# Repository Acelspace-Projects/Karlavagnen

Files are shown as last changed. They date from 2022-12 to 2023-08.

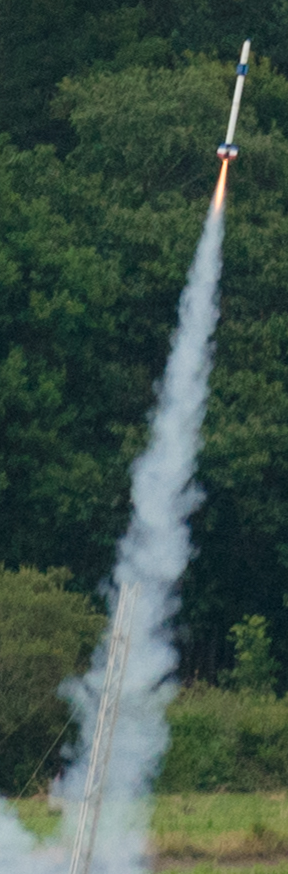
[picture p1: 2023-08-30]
Documentation/RapportDeProjet/img/Decollage.png

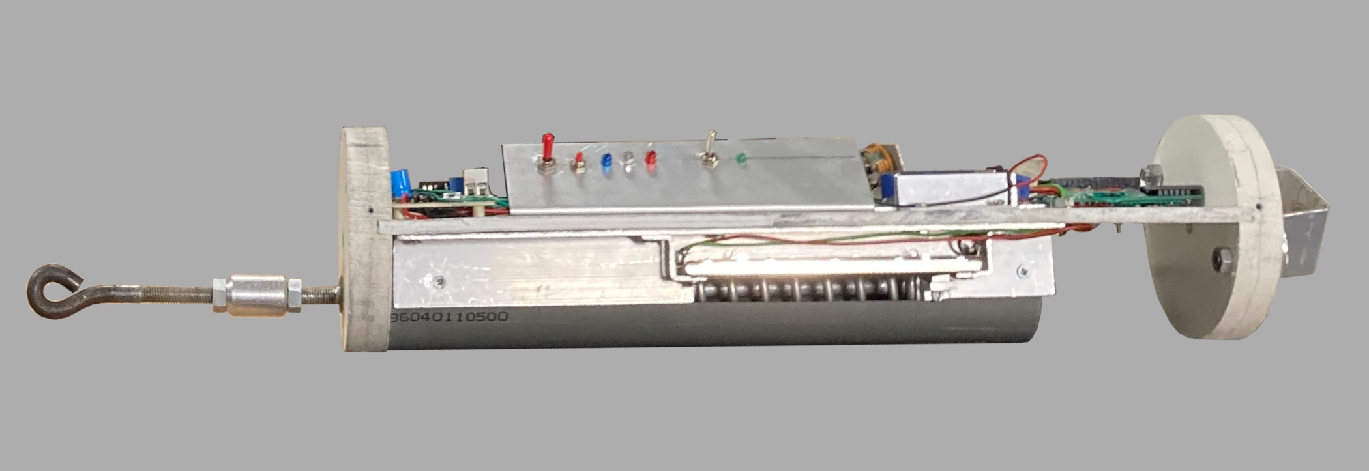
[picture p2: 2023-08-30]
Documentation/RapportDeProjet/img/Electronique1.png

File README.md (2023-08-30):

<h1 align="center">
    <br>
    <a href="https://github.com/Acelspace-Projects/Karlavagnen">
        Acelspace logo
    </a>
    <br>
    <b>Karlavagnen</b>
</h3>

<h3 align="center">
    Ceci est un dépot pour le projet Fusex Karlavagnen utilisé pour le versionning et pour avoir des backups.
</h3>

<div class="badges" align="center">
    
    
</div>

---

### Description
Karlavagnen embarquait en 2023 une expérience de mesure de tension sur les sangles du parachute, deux mesures de vitesse (pitot et venturi), une mesure d'altitude (BMP180), une carte de prise de mesures et de télémesure CATS systems ainsi qu'une caméra intégrée à l'ogive.

### Liens
- [StabTraj](https://github.com/Acelspace-Projects/Karlavagnen/blob/main/Documentation/StabTraj/ST-(StabTraj)_KARLAVAGNEN.xlsx)
- [Dossier de définition](https://github.com/Acelspace-Projects/Karlavagnen/blob/main/Documentation/DossierDeDefinition/DDD_KARLAVAGNEN.pdf)
- [Dossier technique](https://github.com/Acelspace-Projects/Karlavagnen/blob/main/Documentation/DossierTechnique/DT_KARLAVAGNEN.pdf)
- [Rapport de projet](https://github.com/Acelspace-Projects/Karlavagnen/blob/main/Documentation/RapportDeProjet/RP_KARLAVAGNEN.pdf)

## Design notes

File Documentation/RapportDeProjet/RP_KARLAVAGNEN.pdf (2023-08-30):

Rapport de projet | – | Karlavagnen | FX04 | – | 27/08/23

# RAPPORT DE PROJET KARLAVAGNEN

2023

# BENAY Clément CHAUVIN Geoffroy FAJAL Dimitri KAE-NUNE Damien LORIN DE LA GRANDMAISON Alexandre LORIN DE LA GRANDMAISON Clément PINGLIER Etienne

Karlavagnen | FX04 | – | 1/14

# SOMMAIRE

## I. Présenstation de l’équipe ____________ Page 3

1) Présentation générale | Page 3
2) Les membres de l’équipe | Page 3

## II. Présentation de Karlavagnen _________ Page 4 III. Plan Général _______________________ Page 5 IV. Conception mécanique ________________ Page 6

1) Informations générales | Page 6
2) Montage des ailerons | Page 6
3) Système de retenue du propulseur | Page 6

## V. Système d’éjection ___________________ Page 7

1) Plan mécanique | Page 7
2) Plan électrique (séquenceur) | Page 7

## VI. Expériences (Tensionomètre, mesures de vitesse et caméra) ______________________ Page 8

1) Tensionomètre | Page 8
2) Mesures de vitesse | Page 9
3) Caméra | Page 10

## VII. Résultats et exploitation _________ Page 11

1) Rapport de vol | Page 11
2) Exploitation des données | Page 12
1. Caméra: | Page 12
2. Tensionomètre: | Page 12
3. Capteurs de vitesse: | Page 13
4. Capteur de Pression: | Page 13
Karlavagnen | FX04 | – | 2/14

# 1) PRÉSENTATION GÉNÉRALE

Notre groupe était constitué de 7 lycéens issus de 2 lycées de région parisienne (lycée Sonia Delaunay et lycée La Bruyère). Nous étions presque tous en Terminale et un des participant était en Seconde.
Nous avions déjà mené plusieurs projets auparavant dont un projet Fusex nommé OGMA. Chaque membre avait préalablement mené à bien plusieurs projets et avait donc de l’expérience en terme de conception, d’électronique, de mécanique ou même en programmation. Nous étions encadrés par Roger POISSON, vétéran du C’SPACE et habitué des projets fusées et Sylvain BEAU, ingénieur.

# 2) LES MEMBRES DE L’ÉQUIPE

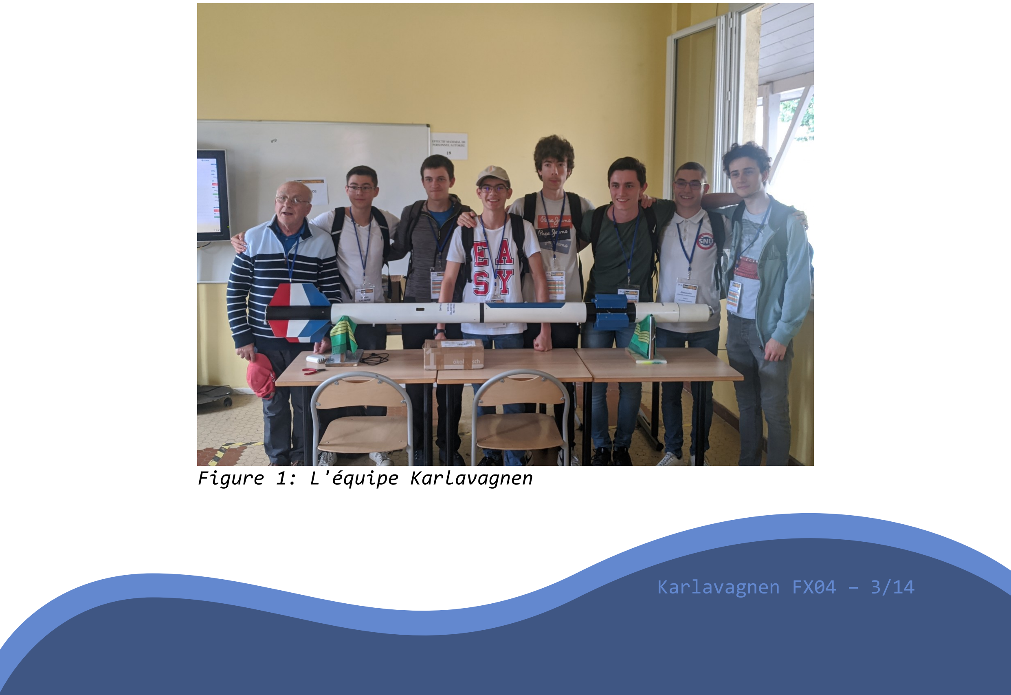
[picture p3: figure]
Karlavagnen; Figure 1: L'équipe Karlavagnen

Le projet KARLAVAGNEN repartait des connaissances acquises avec le projet OGMA, il avait ainsi pour but d’améliorer les expériences qui s’y trouvaient. Cette Fusex contenait donc notament une mesure de la tension aux sangles du parachute (avec le système que l’on a appelé «Tensionomètre»).
Toutefois, de nouvelles expériences ont été ajoutées, avec notamment l’ajout d’un bloc de mesure de vitesse à travers deux manières différentes (pitot et venturi), ainsi que d’une caméra pour filmer l’entièreté du vol. Elle contenait également une carte d’acquisition de mesure et de télémesure “CATS”. Enfin, des mesures d’altitudes ont été effectuées dans le but de les comparer avec les valeurs théoriques de l’altitude données par le StabTraj.

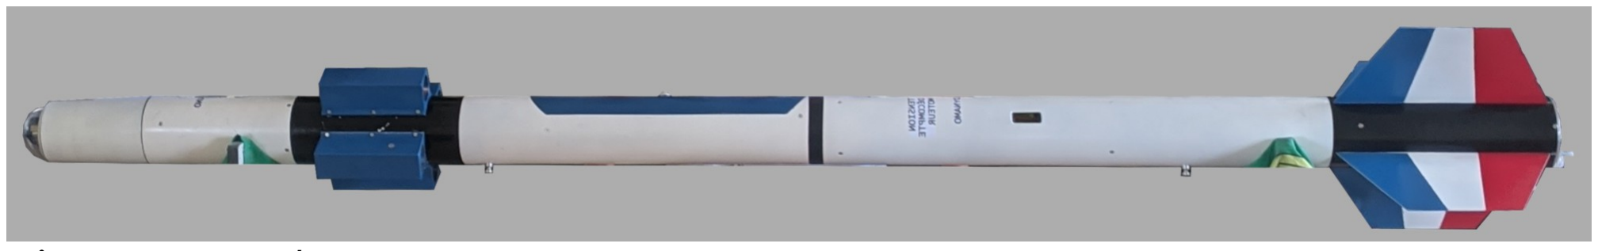
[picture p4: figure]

Figure 2: Karlavagnen

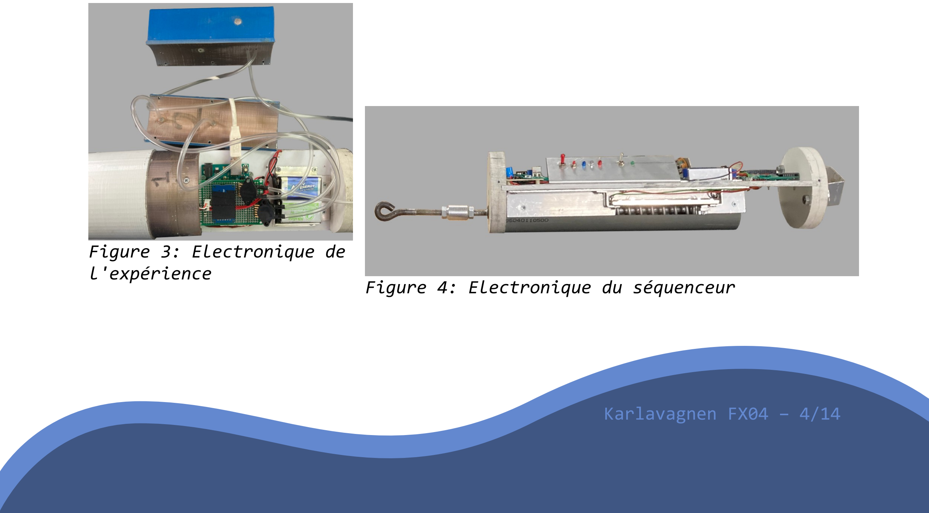
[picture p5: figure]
Karlavagnen; Figure 3: Electronique de l'expérience; Figure 4: Electronique du séquenceur

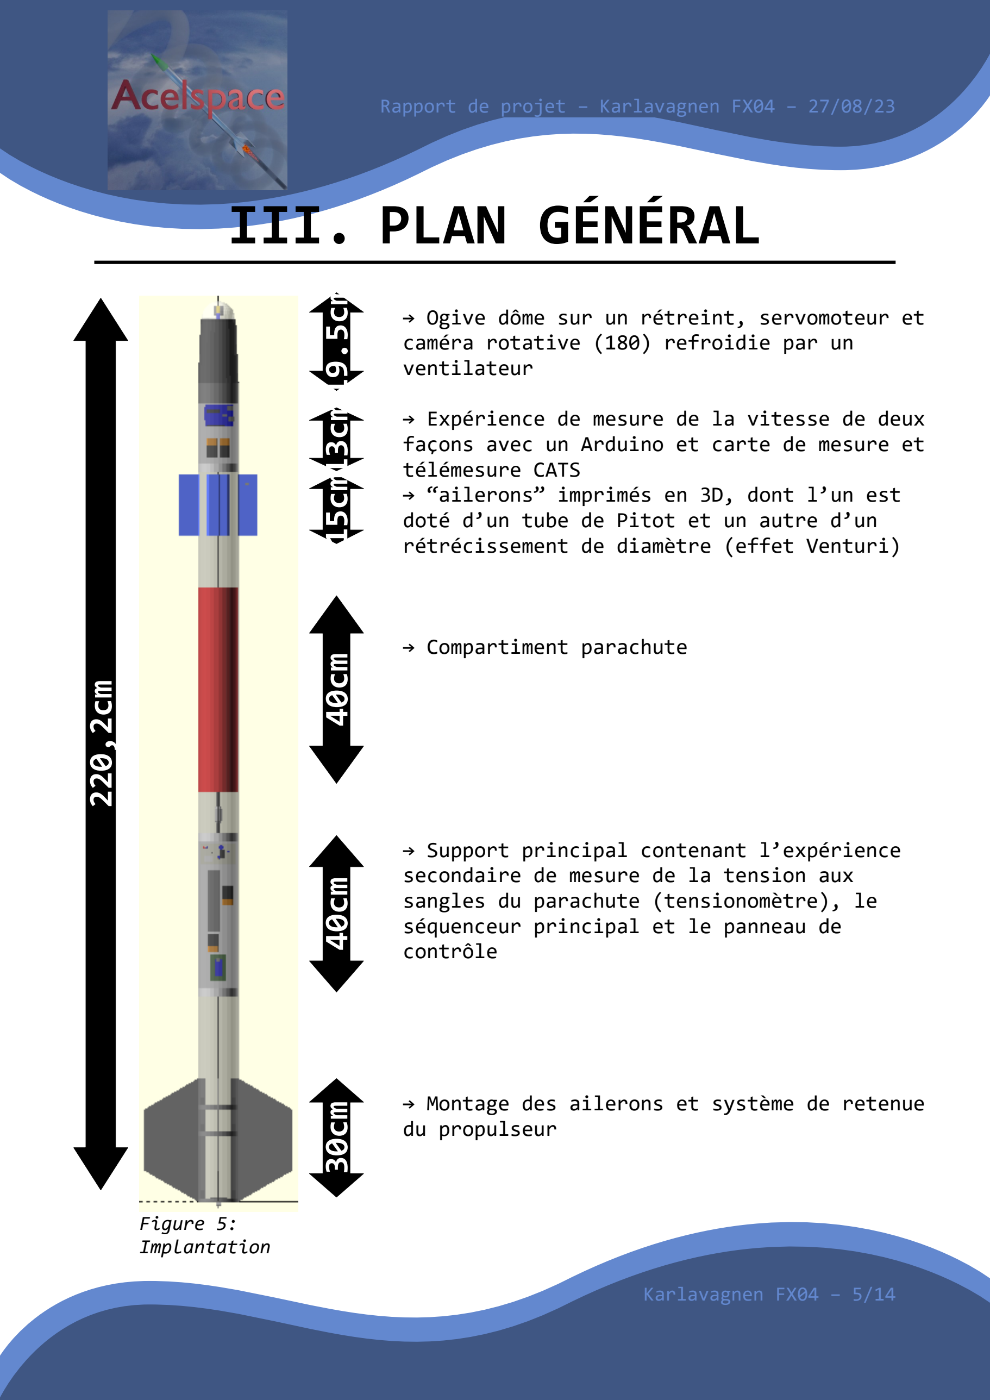
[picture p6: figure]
III. PLAN GÉNÉRAL; Karlavagnen; caméra rotative (180) refroidie par un ventilateur; télémesure CATS; rétrécissement de diamètre (effet Venturi); → Compartiment parachute; → Support principal contenant l’expérience secondaire de mesure de la tension aux sangles du parachute (tensionomètre), le séquenceur principal et le panneau de contrôle; du propulseur; Figure 5: Implantation

→ Ogive dôme sur un rétreint, servomoteur et

→ Expérience de mesure de la vitesse de deux façons avec un Arduino et carte de mesure et

→ “ailerons” imprimés en 3D, dont l’un est doté d’un tube de Pitot et un autre d’un

→ Montage des ailerons et système de retenue

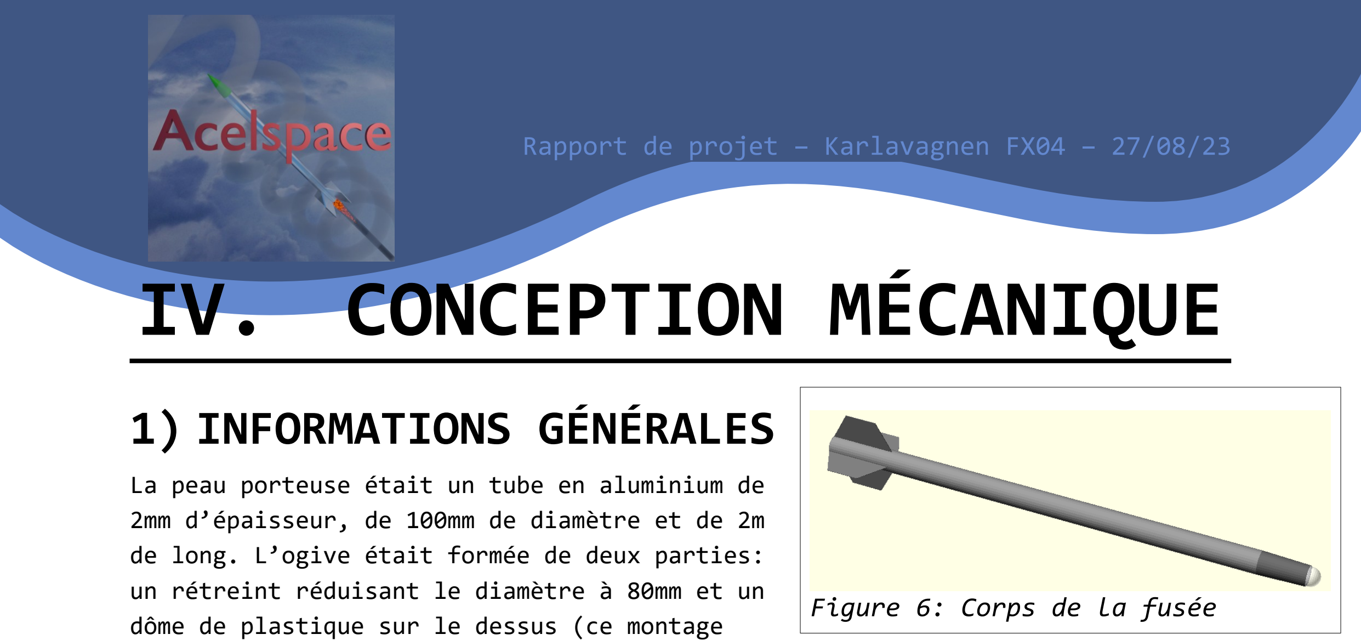
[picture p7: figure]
IV. CONCEPTION MÉCANIQUE; 1) INFORMATIONS GÉNÉRALES; Figure 6: Corps de la fusée

Rapport de projet – Karlavagnen FX04 – 27/08/23

La peau porteuse était un tube en aluminium de 2mm d’épaisseur, de 100mm de diamètre et de 2m de long. L’ogive était formée de deux parties: un rétreint réduisant le diamètre à 80mm et un dôme de plastique sur le dessus (ce montage permettait l’installation de la caméra). Le tout mesurait 19,5 cm en hauteur.

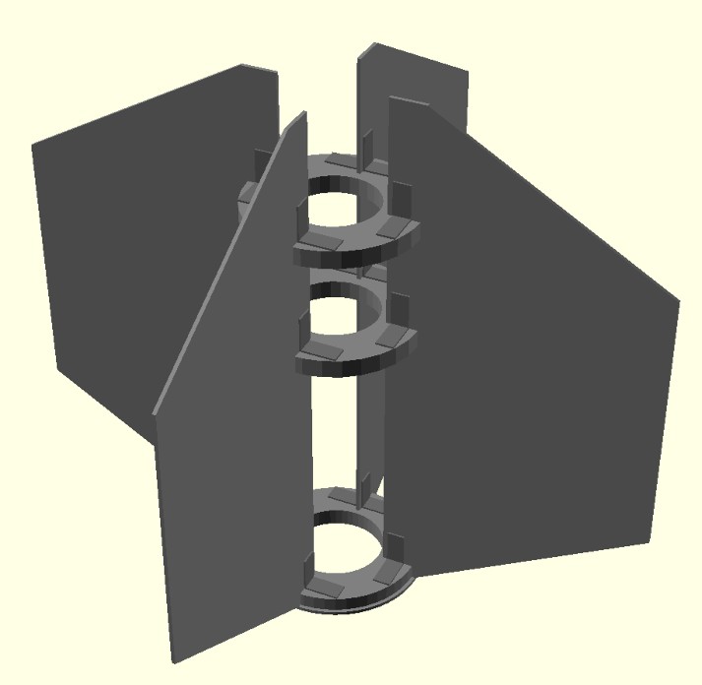
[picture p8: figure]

# 2) MONTAGE DES AILERONS

Les ailerons été attachés à trois bagues en aluminium à l’aide d’équerres de métal.
Le montage complet était accroché au tube avec des vis. La bague la plus inférieure était la plaque de poussée. Elle transférait la poussée du propulseur au corps de la fusée.

# 3) SYSTÈME DE RETENUE DU PROPULSEUR

Le propulseur était retenu par un petit montage en métal accroché à la plaque de poussée.
Celui-ci était construit à l’aide d’un “Sandwich” de pièces en aluminium usinées.
Pour monter le propulseur, il suffisait de l’insérer dans le corps de la fusée. Lorsqu’il était bien monté, un petit “clic” était audible lorsque le pêne ressortait du montage.
Pour enlever le propulseur, il suffisait de pousser la poignée avec le doigt. Étant accroché au pêne il relâchait le propulseur qui pouvait alors être retiré.

Karlavagnen FX04 – 6/14

Figure 8: Sytème de
retenue du propulseur

Pêne

Poignée

Figure 7: Montage des
ailerons

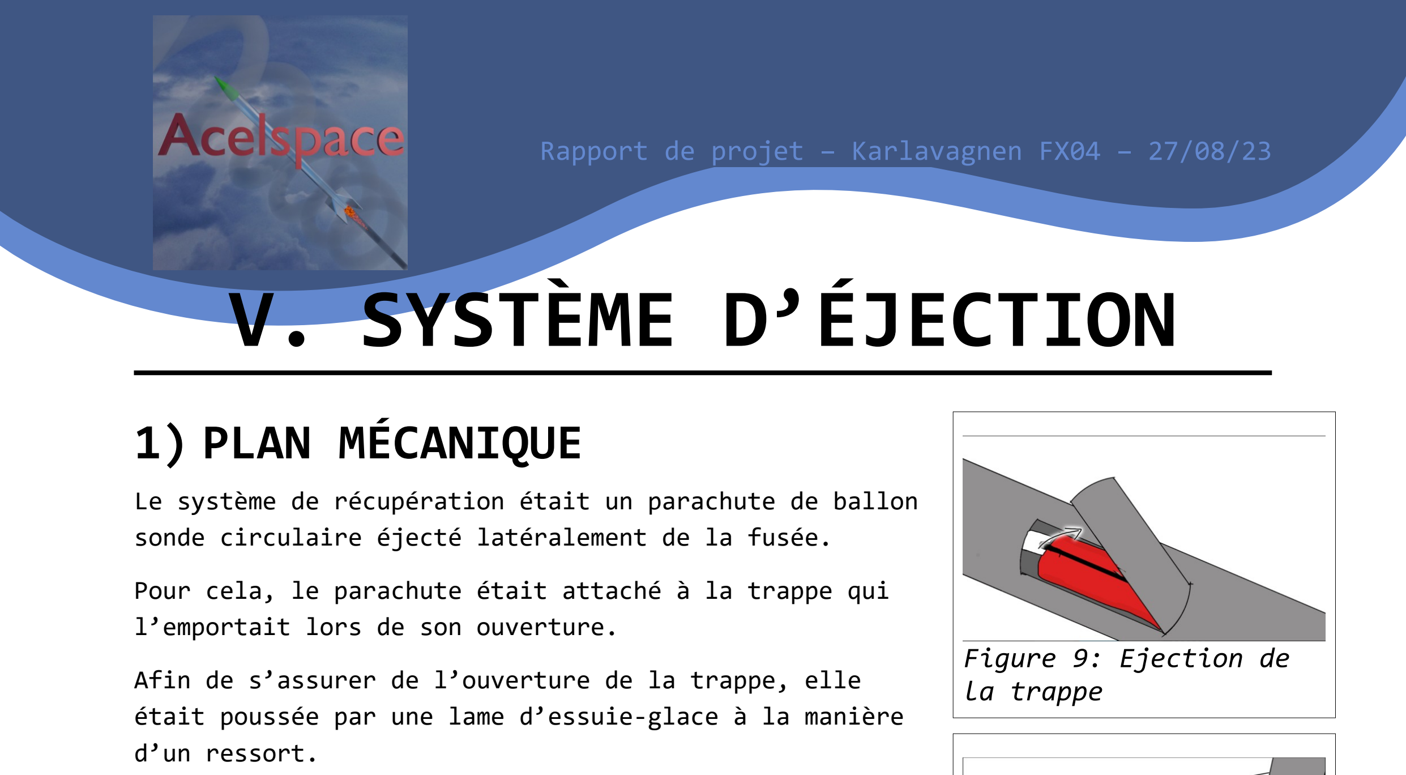
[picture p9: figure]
V. SYSTÈME D’ÉJECTION; 1) PLAN MÉCANIQUE; l’emportait lors de son ouverture.; d’un ressort.; Figure 9: Ejection de la trappe

Le système de récupération était un parachute de ballon sonde circulaire éjecté latéralement de la fusée.
Pour cela, le parachute était attaché à la trappe qui

Afin de s’assurer de l’ouverture de la trappe, elle était poussée par une lame d’essuie-glace à la manière

# 2) PLAN ÉLECTRIQUE (SÉQUENCEUR)

Une minuterie analogique soudée par nos soins permettait
le décompte de l’ouverture de la trappe. Un peu avant
l’apogée, le séquenceur enclenchait un moteur. Sur celui-ci était accroché une cloche qui en tournant libérait alors la trappe.

Figure 10: Sortie du
parachute

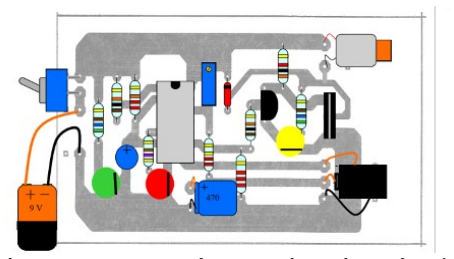
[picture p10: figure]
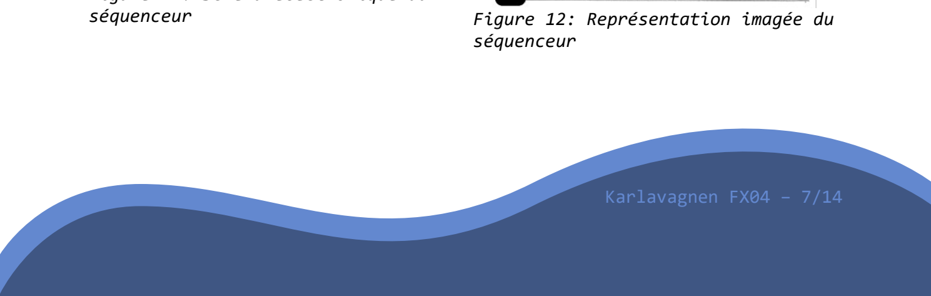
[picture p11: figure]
Karlavagnen; séquenceur; Figure 12: Représentation imagée du

Figure 11: Schéma électronique du

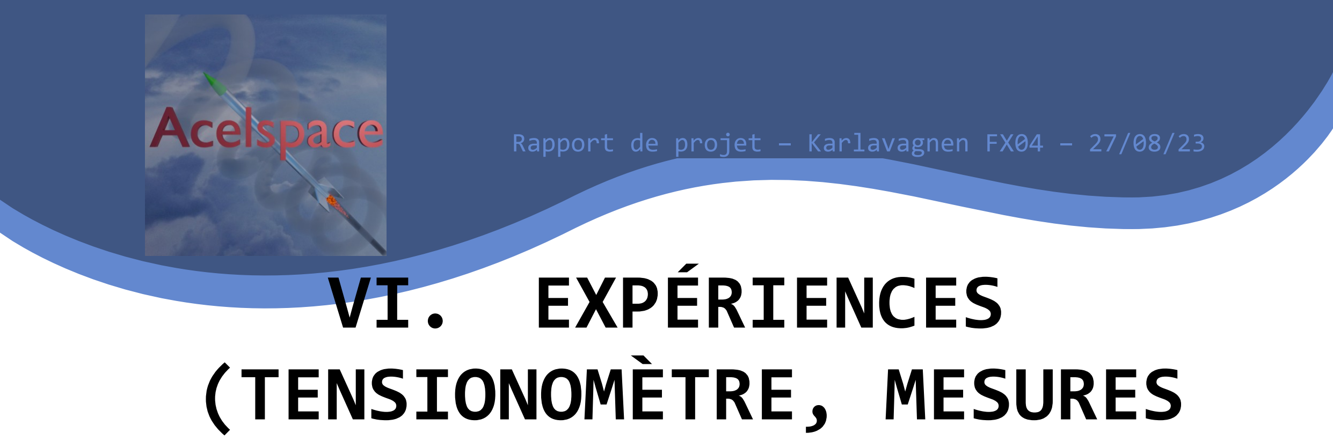
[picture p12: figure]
VI. EXPÉRIENCES (TENSIONOMÈTRE, MESURES

# DE VITESSE ET CAMÉRA)

# 1) TENSIONOMÈTRE

La tension était mesurée sur les sangles du parachute. Deux ressorts de 15cm chacun étaient compressés par la sortie du parachute. Ainsi le potentiomètre linéaire relié à un Arduino permettait d’effectuer l’acquisition des données qui étaient sauvegardées en temps réel sur carte microSD.

Après le vol, les données furent récupérées et passées au travers d’une fonction de conversion qui transformait les données brutes (de 0 à 1023 données par la carte arduino) en données exploitables (force exercée en kg). Celle-ci était déterminée en appliquant des masses connues (poids d’haltère et autres)

Figure 13: Le système est le même que l'an dernier à la différence qu'il sera maintenant composé de deux ressorts pour une plus grande résistance (1000 N) et qu'il n'est plus aligné avec la sangle (il faut maintenant une poulie dans la trappe)

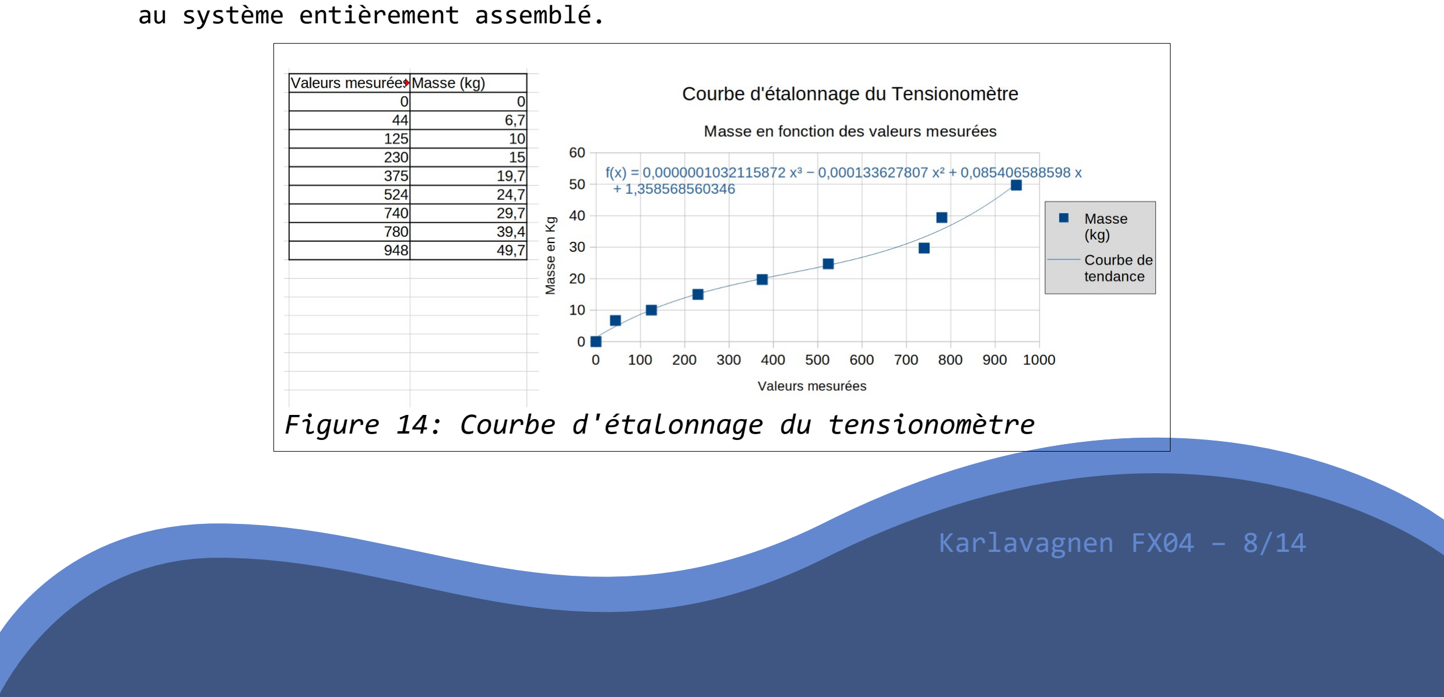
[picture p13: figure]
au système entièrement assemblé.; Karlavagnen

Figure 14: Courbe d'étalonnage du tensionomètre

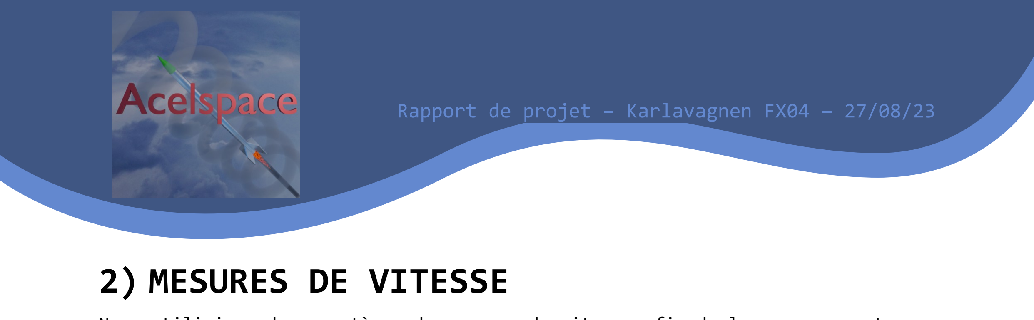
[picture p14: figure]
2) MESURES DE VITESSE

Rapport de projet – Karlavagnen FX04 – 27/08/23

Nous utilisions deux systèmes de mesures de vitesse afin de les comparer. Le premier utilisait un tube de Pitot et le second exploitait l’effet venturi. Les deux systèmes étaient montés sur un support en PVC et les données étaient compilées grâce à une carte Arduino, puis enregistrées sur carte SD.

Sur le tube étaient placés quatre “ailerons” dont deux contenaient les tubes de mesures qui acheminaient l’air jusqu’aux MPX5010DP, capteurs différentiels de pression permettant le calcul de vitesse. Les deux autres permettaient simplement d’assurer la stabilité et étaient passifs.

Figure 17: Tube de
pitot

Figure 15: Tube de
venturi

Figure 16: "Ailerons"
permettant les mesures

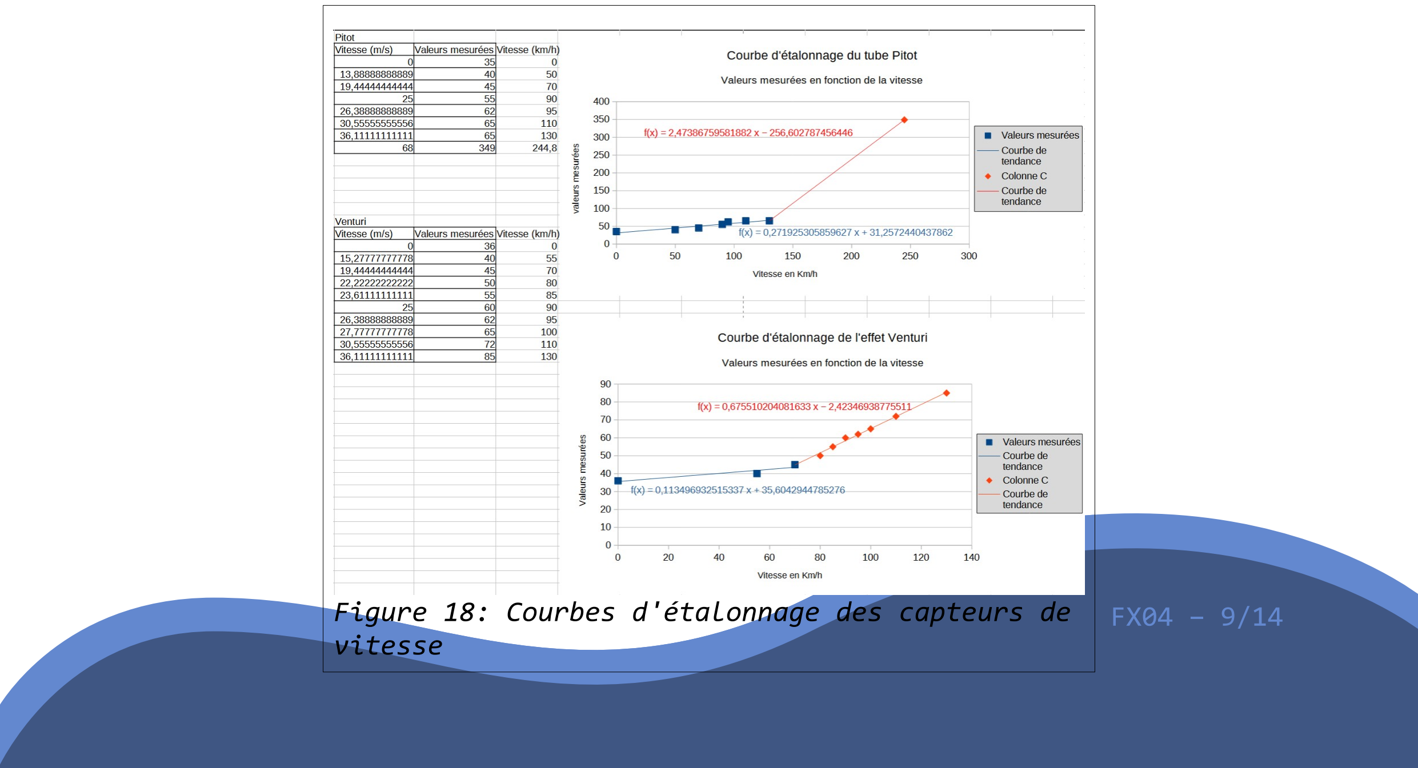
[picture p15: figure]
Karlavagnen; vitesse

Figure 18: Courbes d'étalonnage des capteurs de

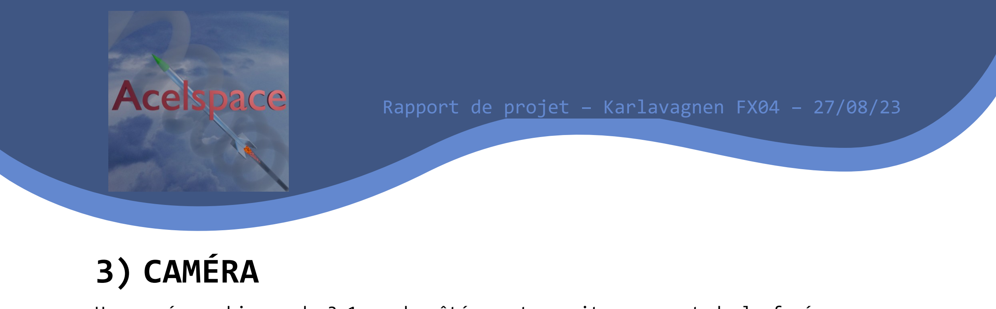
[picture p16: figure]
3) CAMÉRA

Une caméra cubique, de 3.1 cm de côté, se trouvait au sommet de la fusée, protégée par un dôme de plexiglas. Les images ont été enregistrées sur une carte microSD. Un système de servomoteur, faisant des aller-retours entre 0° et 180°, permettait de l’orienter.
Ayant remarqué une perte de performance de la caméra lorsqu’elle surchauffait, nous avions décidé d’installer un ventilateur dans le dôme.

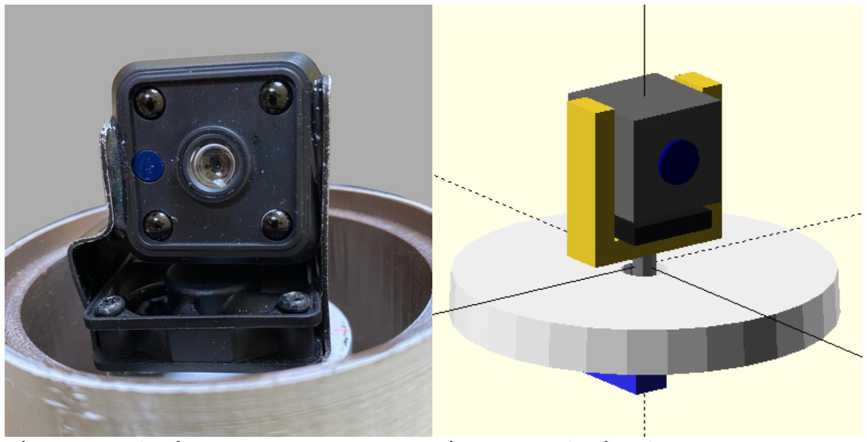
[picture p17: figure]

Figure 19: Caméra IRL | Figure 20: Caméra 3D

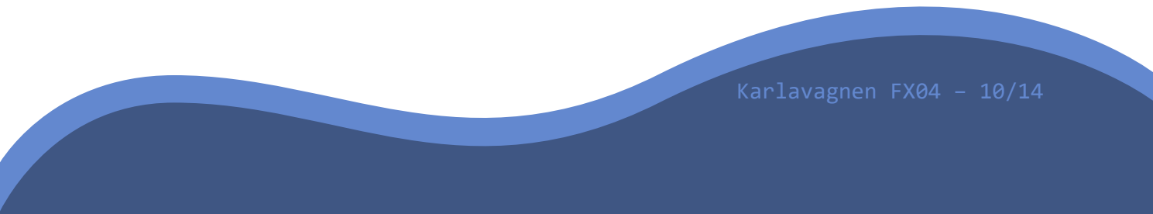
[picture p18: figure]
Karlavagnen

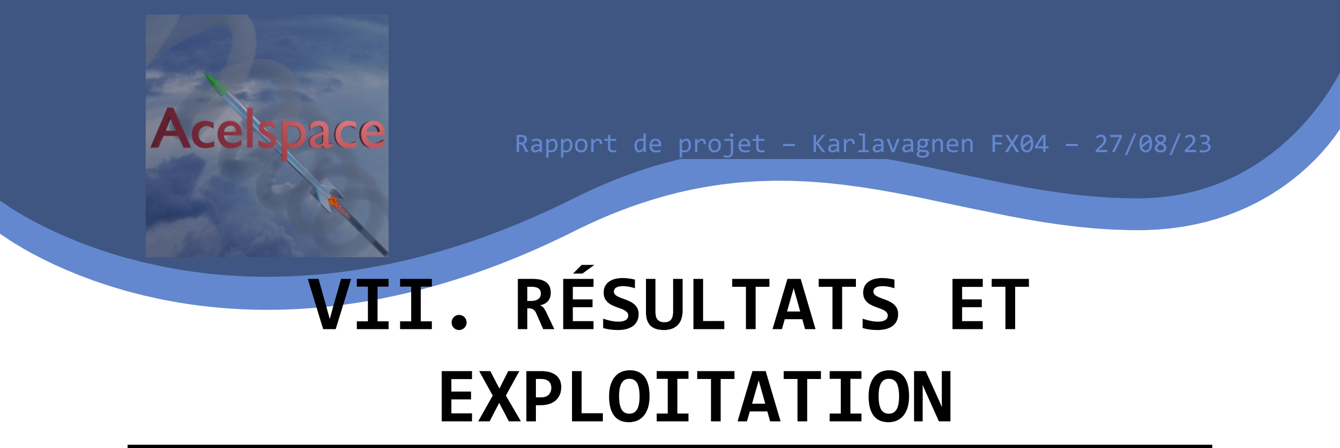
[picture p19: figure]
VII. RÉSULTATS ET EXPLOITATION

# 1) RAPPORT DE VOL

La fusée a été lancée le 19 juillet 2023, le plafond nuageux étant relativement bas, il n’a pas été possible de suivre l’entièreté du vol.
La fusée a cependant effectué un vol nominal et toutes les mesures ont été enregistrées avec succès.
Lors de la récupération, la fusée s’était posée dans un buisson de ronces ce qui l’a amortie à l’atterissage. Grâce à ça, la fusée était donc intacte.

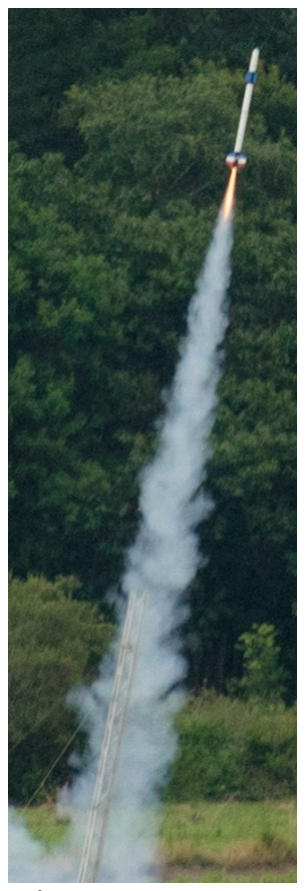
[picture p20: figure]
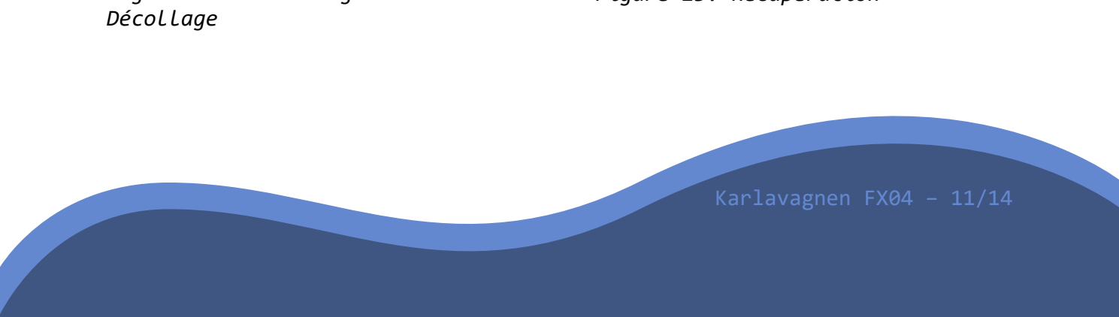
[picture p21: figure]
Karlavagnen; Décollage

Figure 21:

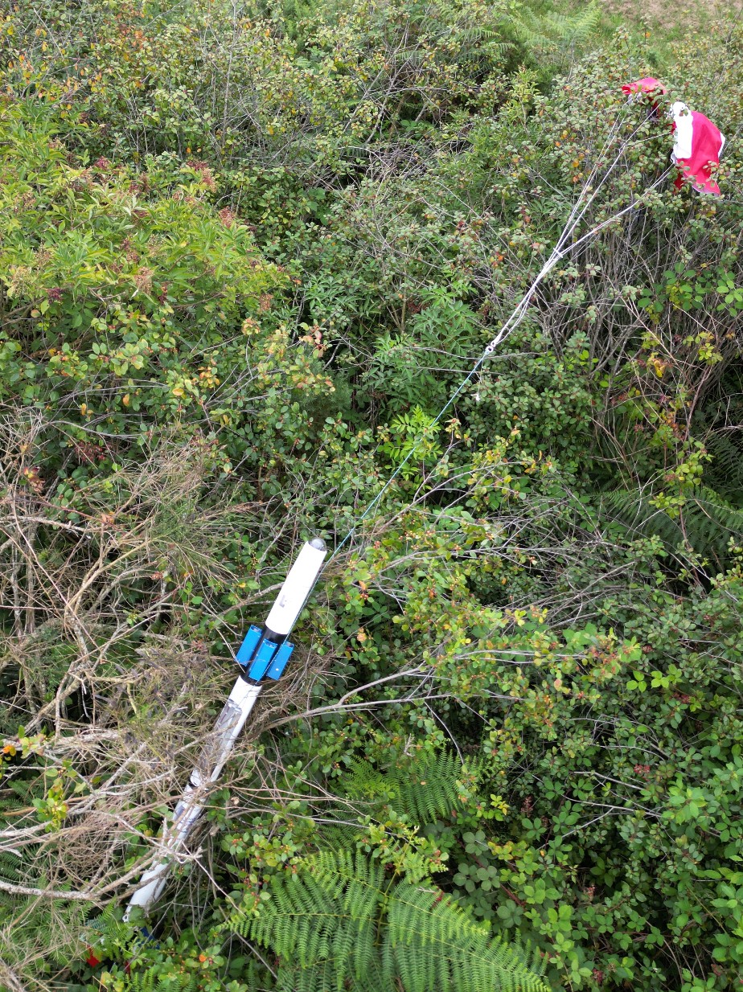
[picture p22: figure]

Figure 22: Descente Figure 23: Récupération

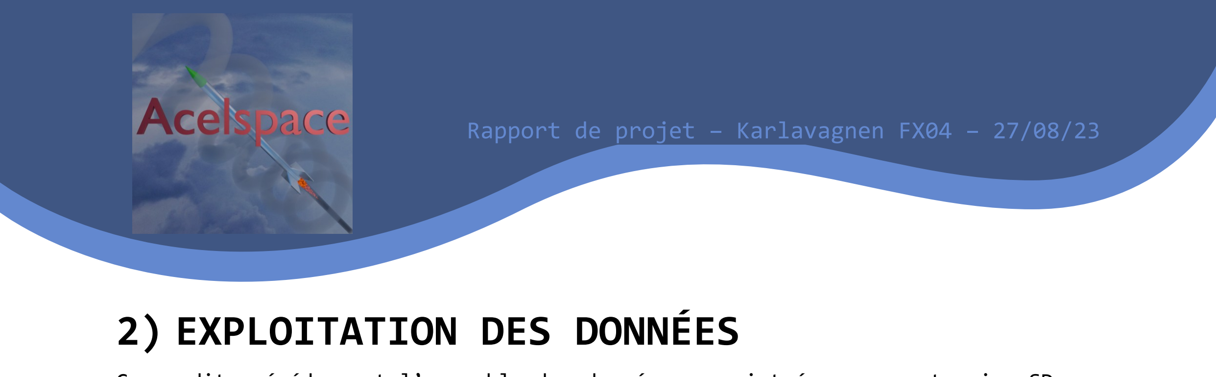
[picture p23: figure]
2) EXPLOITATION DES DONNÉES

Comme dit précédemment l’ensemble des données enregistrées sur carte microSD ont été récupérées. Après utilisation d’un logiciel tableur, les graphes ci-dessous ont été établis.

### 1. CAMÉRA:

La vidéo de la caméra est complète et sans coupures et sectionnée en fichiers de 1 minute (comme prévu). Suite au décollage on peut y voir la fusée monter et s’engouffrer dans les nuages au bout de 8 secondes.

### 2. TENSIONOMÈTRE:

En observant le graphe représentant la force exercée sur les sangles du parachute en fonction du temps écoulé, nous pouvons noter deux choses:
- La vitesse d’acquisition (20Hz) était trop lente et la courbe obtenue présente, en conséquence, un manque de précision lors de la sortie du parachute (deux points seulement montrent l’évolution de la force autour du pic).
- Le capteur a dû être mal dimensionné et en conséquence est arrivé en butée. La valeur max étant 60kg.

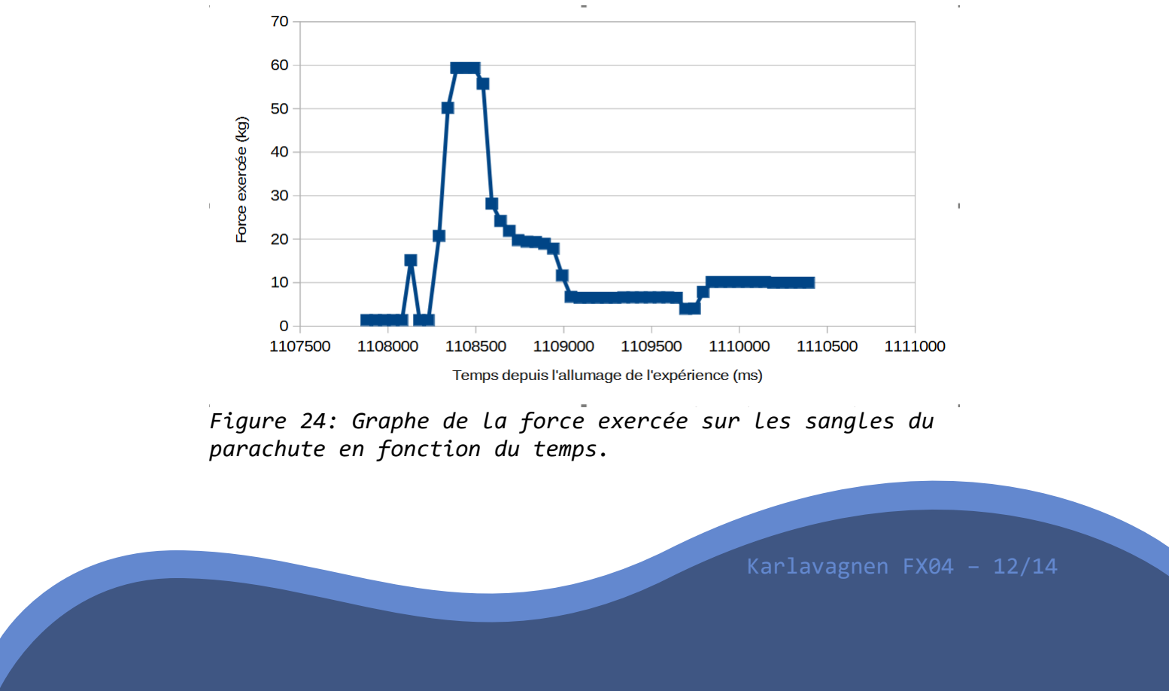
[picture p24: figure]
Karlavagnen; parachute en fonction du temps.

Figure 24: Graphe de la force exercée sur les sangles du

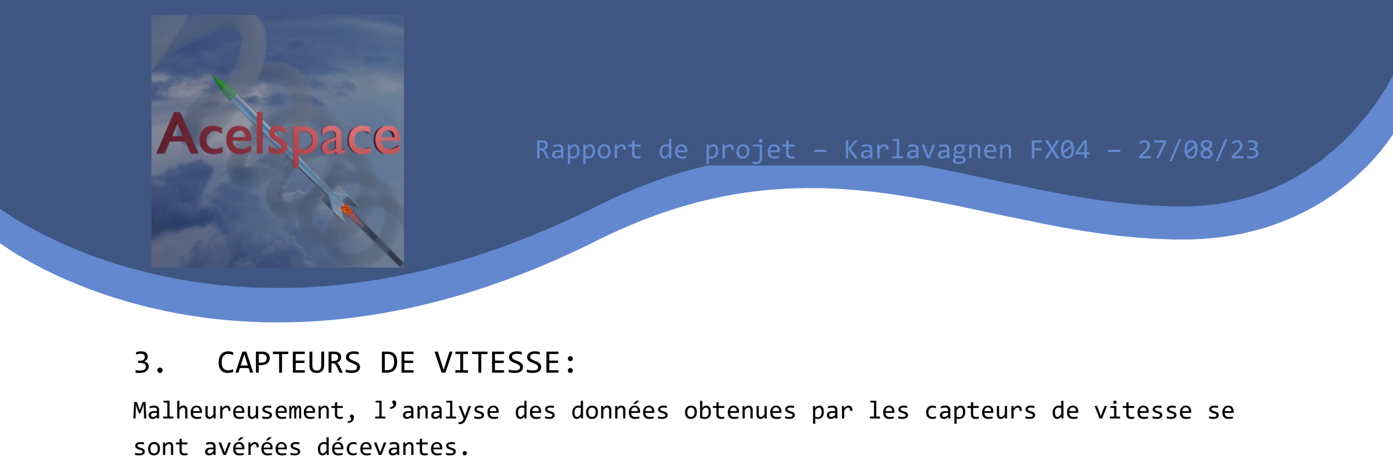
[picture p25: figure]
3. CAPTEURS DE VITESSE:; sont avérées décevantes.

Malheureusement, l’analyse des données obtenues par les capteurs de vitesse se

Tout d’abord le capteur pour la mesure de la vitesse par tube de pitot n’a retourné que des valeurs correspondant à sa butée minimale, ce qui correspond à une erreur de branchement des tuyaux de pression. Pourtant, le sens de branchement était bien connu, mais la présence d’un détrompeur sur le mauvais tuyau a mené un membre de l’équipe à le rebrancher sur la mauvaise entrée du capteur.
Enfin, bien que le capteur utilisant l’effet venturi ait rendu des valeurs, le graphe a révélé la présence de fortes perturbations dans les mesures. Celle-ci sont très probablement liées à des turbulences dans le capteur à cause de la prise aérodynamique des “ailerons”.
L’ensemble des mesures de ces capteurs sont donc inexploitables.

### 4. CAPTEUR DE PRESSION:

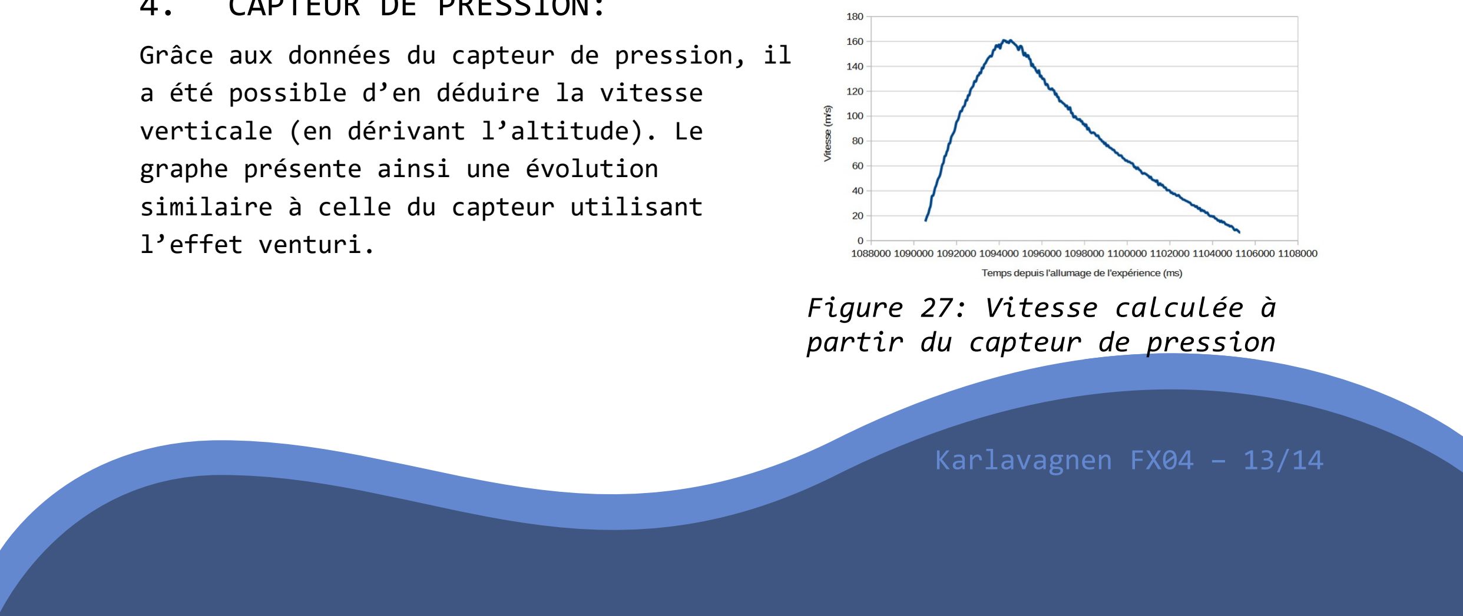
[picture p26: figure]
a été possible d’en déduire la vitesse verticale (en dérivant l’altitude). Le graphe présente ainsi une évolution similaire à celle du capteur utilisant l’effet venturi.; Karlavagnen; Figure 27: Vitesse calculée à partir du capteur de pression

Grâce aux données du capteur de pression, il

Figure 26: Mesures brutes et moyenne à trois points du capteur de Venturi

Figure 25: Mesures brutes du capteur
de Pitot

Le capteur également a pu nous montrer que l’altitude à l’apogée prévue par le StabTraj était grandement surestimée (On s’attendait à une apogée à 1400m mais avons obtenue une apogée à 1200m). Cet écart peut probablement s’expliquer par une mauvaise évaluation du Cx de la fusée, notée à 0.6 dans le StabTraj. Pour faire correspondre les données du StabTraj aux données obtenues il aurait fallu mettre un Cx à 0.85.

# REMERCIEMENTS

“ Karlavagnen est en fait le dernier projet que nous avons réalisé ensemble avant de nous diriger dans nos écoles respectives. Il nous sera donc impossible de réaliser tous ensemble un autre projet.
C’est pour cela que je tenais à remercier tous les membres du groupe de s'être investis dans le projet afin qu'il arrive à complétion. Malgré les problèmes de conception et la difficulté de réalisation, tout le monde a donné de soi et de son temps pour assurer un vol nominal en créant un projet de qualité.
Merci particulièrement à Roger et à Sylvain pour nous avoir accompagnés et aidés lorsque des difficultés se sont présentées, et de nous avoir éclairés de

Et merci à l’équipe de Planète Science de nous avoir permis de vivre ‘une expérience pour les jeunes’. ”, Dimitri FAJAL

Figure 28: Altitude en fonction du temps

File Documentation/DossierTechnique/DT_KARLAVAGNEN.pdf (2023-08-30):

Dossier Technique Karlavagnen – Karlavagnen FX04 – 2023-08-27

# DOSSIER TECHNIQUE KARLAVAGNEN

2023

# FAJAL Dimitri CHAUVIN Geoffroy LORIN DE LA GRANDMAISON Clément LORIN DE LA GRANDMAISON Alexandre BENAY Clément KAE-NUNE Damien PINGLIER Etienne

Karlavagnen FX04 – 1/8

# SOMMAIRE

## I. Plan général _________________________ Page 3 II. Conception mécanique ________________ Page 4

1) Informations générales | Page 4
2) Montage ailerons | Page 4
3) Système de retenue du propulseur | Page 4

## III. Système d’éjection _________________ Page 5

1) Plan mécanique | Page 5
2) Plan électrique (séquenceur) | Page 5

## IV. Expériences (Tensionomètre, mesures de vitesse et caméra) ______________________ Page 6

1) Tensionomètre | Page 6
2) Mesures de vitesse | Page 7
3) Caméra | Page 7

# I. PLAN GÉNÉRAL

Xmm; Figure 1: Implantation

→ Ogive dôme sur un rétreint, servomoteur et caméra rotative (180) soutenue par un ventilateur

→ Minuterie secondaire : Arduino xpérience de mesure de la vitesse de deux façons afin de les comparer

→ Parallélépipèdes imprimés en 3D, dont l’un est doté d’un tube de Pitot et un autre d’un rétrécissement de diamètre (effet Venturi)

→ Trappe d’éjection du parachute

→ Support principal contenant l’expérience secondaire de mesure de la tension aux sangles du parachute (tensionomètre), le séquenceur principal et le panneau de contrôle

→ Montage des ailerons et système de retenue du propulseur

Nous utilisons un total de 5 piles 9V : trois dans la minuterie secondaire et deux dans la minuterie principale.

# II. CONCEPTION MÉCANIQUE

# 1) INFORMATIONS GÉNÉRALES

La peau porteuse est un tube en aluminium de 2mm d’épaisseur, de 100mm de diamètre et de 2m de long. Elle offre une grand solidité. L’ensemble des montages à l’intérieur sont solidement
accroché au tube par des vis.


L’ogive est formée de deux parties : un rétreint réduisant le diamètre à 80mm et un dôme de plastique sur le dessus (ce montage permet l’installation d’une caméra). Le tout mesure 19,5 cm en hauteur.


# 2) MONTAGE AILERONS

Les ailerons sont attachés à trois bagues en aluminium à l’aide d’équerres de métal.
Le montage complet est accroché au tube par avec des vis. La bague la plus inférieure est la plaque de poussée.
Elle transfère la poussée du propulseur au corps de la
fusée.

# 3) SYSTÈME DE RETENUE DU PROPULSEUR

Le propulseur est retenu par un petit montage en métal
accroché à la plaque de poussée.
Celui-ci est construit à l’aide d’un « Sandwich » de pièces en aluminiums usinées.
Pour monter le propulseur, il suffit de l’insérer dans le corps de la fusée. Lorsqu’il est bien montée, un petit « clic » est audible lorsque la pêne ressort du montage.
Pour enlever le propulseur, il faut pousser la poignée avec le doigt. Étant accroché à la pêne il relâchera le propulseur qui peut alors être retiré.

Pêne

Figure 4: Sytème de retenue du propulseur

Poignée

Figure 3: Montage des
ailerons

Figure 2: Corps de la fusée

# III. SYSTÈME D’ÉJECTION

# 1) PLAN MÉCANIQUE

Le système de récupération est un parachute de ballon sonde circulaire éjecté latéralement de la fusée. Pour cela, il est attaché à la trappe qui l’emporte lors de son ouverture. Afin de s’assurer de l’ouverture de la


trappe, elle est poussée par une lame d’essuie-glace à la manière d’un ressort.

# 2) PLAN ÉLECTRIQUE (SÉQUENCEUR)

Une minuterie analogique soudée par nos soins permet le décompte de l’ouverture de la trappe. Un peu avant


l’apogée, le séquenceur enclenche un moteur. Sur celui-ci est accroché une cloche qui en tournant libère la trappe.

Figure 5: Ejection de la
trappe

Figure 6: Sortie du
parachute


Figure 7: Schéma électronique du


séquenceur | Figure 8: Représentation imagée du séquenceur

# IV. EXPÉRIENCES (TENSIONOMÈTRE, MESURES DE VITESSE ET CAMÉRA)

# 1) TENSIONOMÈTRE

La tension sera mesurée sur les sangles du parachute. Deux ressorts de 15cm chacun sont compressés par de la sortie du parachute. Ainsi le potentiomètre linéaire relié à un Arduino permettent d’effectuer l’acquisition des données qui sont sauvegardées en temps réel sur carte microSD.

Après vol, les données sont récupérées et passées au travers d’une fonction de conversion qui transforme les données brutes (de 0 à 1023 données par la carte arduino) en donées exploitables (force exercée en kg).
Cette fonction de conversion est déterminée en appliquant des masses connues (poids d’altère et autres) au système entièrement assemblé. Une courbe d’étalonnage est alors établie sur un tableur pour ensuite faire apparaître la courbe de tendance dont l’équation est la fonction de conversion.

Figure 9: Le système est le même que l'an dernier à la différence qu'il sera maintenant composé de deux ressorts pour une plus grande résistance (1000 N) et qu'il n'est plus aligné avec la sangle (il faut maintenant une poulie dans la trappe)


Figure 10: Courbe d'étalonnage du tensionomètre

# 2) MESURES DE VITESSE

Nous utilisons deux systèmes de mesures de vitesse afin de les comparer. Le premier utilise un tube de Pitot et le second exploite l’effet venturi. Les deux systèmes sont montés sur un support en PVC et les données sont compilées grâce à une carte Arduino, puis enregistrées sur carte SD.


Sur le tube sont placé quatre « ailerons » dont deux d’entre eux contiennent les tubes de mesures qui acheminent l’air jusqu’aux MPX5010DP, capteurs différentiels de pression permettant le calcul de vitesse. Les deux autres permettent simplement d’assurer la stabilité et sont passifs.

Figure 14: Tube de
pitot

Figure 11: Tube de
venturi

Figure 13: "Ailerons"
permettant les mesures


Figure 12: Courbes d'étalonnage des capteurs de vitesse

# 3) CAMÉRA

Une caméra cubique, de 3.1 cm de côté, se trouve au sommet de la fusée, protégée par un dôme de plexiglas. Les images seront enregistrées sur une carte microSD et pourront être récupérées après le vol. Un système de servomoteur, faisant des allers-retours entre 0° et 180°, permet de l’orienter.
Ayant remarqué une perte de performance de la caméra lorsqu’elle surchauffait, nous avons décidé d’installer un ventilateur dans le dôme.


Figure 15: La caméra

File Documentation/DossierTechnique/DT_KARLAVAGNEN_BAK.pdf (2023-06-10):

Dossier Technique Karlavagnen – Karlavagnen FX04 – 04/06/23

# DOSSIER TECHNIQUE KARLAVAGNEN

2023

# FAJAL Dimitri CHAUVIN Geoffroy LORIN DE LA GRANDMAISON Clément LORIN DE LA GRANDMAISON Alexandre BENAY Clément KAE-NUNE Damien PINGLIER Etienne

Karlavagnen FX04 – 1/7

# SOMMAIRE

## I. Plan général _________________________ Page 3 II. Conception mécanique ________________ Page 4

1) Informations générales | Page 4
2) Montage ailerons | Page 4
3) Système de retenue du propulseur | Page 4

## III. Système d’éjection _________________ Page 5

1) Plan mécanique | Page 5
2) Plan électrique (séquenceur) | Page 5

## IV. Exp principale (contrôle du roulis) _ Page 6

1) Explication | Page 6
2) Électronique | Page 6
3) Mécanique des ailerons | Page 6

## V. Exp secondaires (Tensionomètre, mesures de vitesse et caméra) ______________________ Page 7

1) Tensionomètre | Page 7
2) Mesures de vitesse | Page 7
3) Caméra | Page 7

# I. PLAN GÉNÉRAL

Xmm; Figure 1: Implantation

→ Ogive dôme sur un rétreint et caméra rotative (360)

→ Expérience secondaire de mesure de la vitesse de deux façon afin de les comparer

→ Expérience principale de contrôle du roulis (arduino + IMU)

→ Trappe d’éjection du parachute

→ Support principal contenant l’expérience secondaire de mesure de la tension aux sangles du parachute (tensionomètre), le séquenceur principal et le panneau de contrôle

→ Montage aileron et système de retenue du propulseur

# II. CONCEPTION MÉCANIQUE

# 1) INFORMATIONS GÉNÉRALES

La peau porteuse est un tube en aluminium de 2mm d’épaisseur, de 100mm de diamètre et de 2m de long. Elle offre une grand solidité. L’ensemble des montages à l’intérieur sont solidement
accroché au tube par des vis.


L’ogive est formée de deux parties : un rétreint réduisant le diamètre à 80mm et un dôme de plastique sur le dessus (ce montage permet l’installation d’une caméra)

# 2) MONTAGE AILERONS

Les ailerons sont attachés à trois bagues en aluminium à l’aide d’équerres de métal.
Le montage complet est accroché au tube par avec des vis. La bague la plus inférieure est la plaque de poussée.
Elle transfère la poussée du propulseur au corps de la
fusée.


# 3) SYSTÈME DE RETENUE DU PROPULSEUR

Le propulseur est retenu par un petit montage en métal
accroché à la plaque de poussée.
Celui-ci est construit à l’aide d’un « Sandwich » de pièces en aluminiums usinées.
Pour monter le propulseur, il suffit de l’insérer dans le corps de la fusée. Lorsqu’il est bien montée, un petit « clic » est audible lorsque la pêne ressort du montage.
Pour enlever le propulseur, il faut pousser la poignée avec le doigt. Étant accroché à la pêne il relâchera le propulseur qui peut alors être retiré.

Pêne

Figure 4: Sytème de retenue du propulseur

Poignée

Figure 3: Montage des
ailerons

Figure 2: Corps de la fusée

# III. SYSTÈME D’ÉJECTION

# 1) PLAN MÉCANIQUE

Le système de récupération est un parachute de ballon sonde circulaire éjecté latéralement de la fusée. Pour cela, il est attaché à la trappe qui l’emporte lors de son ouverture. Afin de s’assurer de l’ouverture de la


trappe, elle est poussée par une lame d’essuie-glace à la manière d’un ressort.

# 2) PLAN ÉLECTRIQUE (SÉQUENCEUR)

Une minuterie analogique soudée par nos soins permet le décompte de l’ouverture de la trappe. Un peu avant


l’apogée, le séquenceur enclenche un moteur. Sur celui-ci est accroché une cloche qui en tournant libère la trappe.


Figure 7: Schéma du séquenceur

Figure 5: Ejection de la
trappe

Figure 6: Sortie du
parachute

# IV. EXP PRINCIPALE (CONTRÔLE DU ROULIS)

# 1) EXPLICATION

L’expérience principale consiste à contrôler le roulis à l’aide d’un gyroscope relié à une carte électronique contrôlant des ailerons placés sur la partie supérieure du tube.

# 2) ÉLECTRONIQUE

Le gyroscope permet les mesures à travers l’utilisation d’une carte Arduino. Ces mesures sont utilisées pour le calcul des actions à effectuer sur le moteur contrôlant les ailerons. Elles servent aussi à décider de l’orientation de la caméra et les mesures sont enregistrées sur carte microSD.

# 3) MÉCANIQUE DES AILERONS

Un ensemble d’engrenages entraînés par un moteur permettent la mise en rotation des ailerons. Ceux-ci tournent alors légèrement pour modifier le roulis de la fusée.


Figure 8: Arduino pour
l'expérience du roulis


Figure 9: Système
d'engrenages

# V. EXP SECONDAIRES (TENSIONOMÈTRE, MESURES DE VITESSE ET CAMÉRA)

# 1) TENSIONOMÈTRE

La tension sera mesurée sur les sangles du parachute. Deux ressort de 15cm chacun sont compressés par de la sortie du parachute. Ainsi le potentiomètre linéaire relié à un Arduino permettent d’effectuer l’acquisition des données qui sont sauvegardées en temps réel sur carte microSD.

# 2) MESURES DE VITESSE

Nous utilisons deux systèmes de mesures de la vitesse afin de les comparer. Le premier utilise un tube de Pitot et le second exploite l’effet venturi. Les deux systèmes sont montés sur un support en PVC et les données sont compilées grâce à une carte Arduino.

# 3) CAMÉRA

Une mini-caméra cubique, de 2.3 cm de côté, se trouve au sommet de la fusée, protégée par un dôme de plastique. Les images seront enregistrées sur une carte microSD et pourront être exploitées après le vol. Un système de servomoteurs, pilotés par Arduino permettent de l’orienter.


Figure 11: La caméra

Figure 10: Le système est le même que l'an dernier à la différence qu'il sera maintenant composé de deux ressorts pour une plus grande résistance et qu'il n'est plus aligné avec la sangle (il faut maintenant une poulie dans la trappe)

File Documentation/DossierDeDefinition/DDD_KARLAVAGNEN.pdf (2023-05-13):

Dossier de définition – Karlavagnen – 2022-2023

# DOSSIER DE DÉFINITION KARLAVAGNEN

2022-2023

# BENAY Clément CHAUVIN Geoffroy FAJAL Dimitri KAE-NUNE Damien LORIN DE LA GRANDMAISON Alexandre LORIN DE LA GRANDMAISON Clément PINGLIER Etienne

Karlavagnen – 1/10

# SOMMAIRE

## Présentation de l’équipe ________________ Page 3

Présentation générale | Page 3
Les membres de l’équipe | Page 3

## Présentation de OGMA ____________________ Page 4 Présentation de KARLAVAGNEN _____________ Page 5

Objectifs | Page 5
Comparaison avec Ogma | Page 5

## Expérience du contrôle de roulis ________ Page 6 Mesure de la tension des sangles du parachute «Le tensionomètre» ______________________ Page 7 Caméra montée sur axe rotatif ___________ Page 8 Mesure de l’altitude et gyroscope _______ Page 9 Mesure de la vitesse ___________________ Page 10

par tube Pitot | Page 10
par effet Venturi | Page 10
Comparaison | Page 10

# PRÉSENTATION DE L’ÉQUIPE

# PRÉSENTATION GÉNÉRALE

Notre groupe est constitué de 7 lycéens issus de 2 lycées de région parisienne (lycée Sonia Delaunay et lycée La Bruyère). Nous sommes répartis en Terminale et Seconde (de 15 à 17 ans). Nous avons déjà mené plusieurs projets auparavant dont un projet Fusex ensemble : OGMA. Chaque membre a mené à bien plusieurs projets et a donc de l’expérience en terme de conception, d’électronique, de mécanique ou même en programmation. Nous sommes encadrés par Roger POISSON, vétéran du C’SPACE et habitué des projets fusées et Sylvain BEAU, ingénieur.

# LES MEMBRES DE L’ÉQUIPE

Geoffroy CHAUVIN : élève de Terminale au lycée La Bruyère de Versailles. 6 projets à son actif dont un projet Fusex, OGMA.

### Clément LORIN DE LA GRANDMAISON : élève de Seconde au lycée Sonia

Delaunay à Villepreux. 4 projets à son actif.

### Clément BENAY, Damien KAE-NUNE, Etienne PINGLIER, Alexandre LORIN DE LA GRANDMAISON, Dimitri FAJAL : élèves de Terminale au

lycée Sonia Delaunay à Villepreux. Nous avons chacun réalisé 5 projets et avons travaillé l'année dernière sur le projet Fusex OGMA.
Le chef de projet pour le projet de cette année est Dimitri FAJAL.

# PRÉSENTATION DE OGMA

OGMA est le projet que nous avons mis en œuvre durant la campagne de lancement 2021-2022 et qui a abouti à un vol nominal. Le but du projet était de limiter le roulis par un système passif à l’aide de masselottes. Nous avons décidé de réitérer l’expérience afin d’améliorer les résultats de l’année passée. Cependant, nous avons décidé de changer le système de contrôle de roulis pour un système avec des ailerons. En revanche, le système de mesure de tension aux sangles du parachute sera le même mais sera revu pour être adapté à la charge prévue, ce qui n’était malheureusement pas le cas l’année dernière, le ressort sera donc agrandi afin de pouvoir encaisser un plus grand choc.


Illustration 1: Groupe du projet OGMA

# PRÉSENTATION DE KARLAVAGNEN

# OBJECTIFS

KARLAVAGNEN est le nouveau projet Fusex que nous allons mettre en œuvre cette année. Le projet KARLAVAGNEN repart des connaissances acquises avec le projet OGMA mais est réalisé à partir de zéro, il a pour but d’améliorer les expériences précédentes. Cette Fusex va donc réitérer la mesure de la tension aux sangles du parachute (avec le système que l’on va appeler maintenant «Tensionomètre»). Toutefois, de nouvelles expériences vont être ajoutées, avec notamment l’ajout d’une caméra pour filmer l’entièreté du vol et un système de contrôle du roulis totalement revisité et amélioré ainsi qu’un tube de Pitot pour mesurer la vitesse de la Fusex. Cette vitesse sera aussi mesuré via l’effet Venturi. Les deux mesures obtenues seront comparées afin de vérifier la fiabilité et l’incertitude de ces mesures. Un gyroscope sera aussi nécessaire afin de s’assurer que le système de contrôle du roulis aura bien fonctionné. Enfin, des mesures d’altitude seront effectuées dans le but de les comparer avec les valeurs théoriques de l’altitude données par le StabTraj.

# COMPARAISON AVEC OGMA

La Fusex reprendra presque à l’identique les dimensions de la Fusex de l’année dernière, à savoir un tube de 2m de haut et de diamètre de 10cm. En revanche, l’ogive sera bien différente puisqu’elle sera munie d’un dôme transparent qui permettra l’intégration de la caméra. De même, le système de contrôle du roulis changera puisque nous passerons de bras à des ailerons.

# EXPÉRIENCE DU CONTRÔLE DE ROULIS

Cette expérience a pour but de contrôler le roulis, c’est à dire limiter le nombre de tours que la fusée va faire sur elle même au cours du vol. Pour ce faire, nous allons mettre en place un système de deux ailerons placés sur un axe rotatif chacun. Ces derniers bougeront de manière opposée afin de ne pas modifier la trajectoire. Ce système remplacera notre ancien système de masselottes afin d’accroître l’efficacité de ces derniers qui ne nous donnaient pas entière satisfaction. Nous comptons donc tester de nouveau cette expérience.


Illustration 2: Ancien Système


Illustration 3: Modélisation prototype du nouveau système (à titre illustratif)

# MESURE DE LA TENSION DES SANGLES DU PARACHUTE «LE TENSIONOMÈTRE»

Nous réitérons cette expérience afin d’obtenir de meilleurs résultats quant à la réelle tension exercée sur les sangles du parachute. Le parachute est relié à une tige qui compresse le ressort lors de la sortie du parachute. Cette compression modifie la position du potentiomètre linéaire attaché au ressort. Les changements de tensions sont ainsi enregistrées par un Arduino au cours du vol. Cependant, cette année, le ressort sera allongé afin de pouvoir encaisser un plus grand choc et avoir des mesures plus précises.


Illustration 4: Le "Tensionomètre" de OGMA

# CAMÉRA MONTÉE SUR AXE ROTATIF

Pour la première fois, nous allons incorporer une caméra FPV (Caméra avec angle de vue classique) afin de filmer l’entièreté du vol dans le but d’avoir une preuve du contrôle du roulis ainsi qu’une vidéo du de la fusée (car c’est joli). Un servomoteur permettra la rotation de cette caméra afin de filmer tous les angles de la fusée (d’où l’appellation caméra 360°).


Illustration 5: Schéma prototype du système (à titre illustratif)

# MESURE DE L’ALTITUDE ET GYROSCOPE

Grâce à un Arduino, nous allons mesurer l’altitude pour compléter nos mesures. Le gyroscope, lui, servira pour le contrôle du roulis. Il nous fournira des mesures en temps réel qui seront analysées en direct par un Arduino qui transmettra alors la rotation que doivent faire les ailerons au moteur de l’axe rotatif de ces derniers. Il permettra un contrôle du roulis autonome et immédiat, ainsi qu’actif ce que ne faisait pas le système de masselottes de OGMA.


Illustration 6: Arduino utilisé pour OGMA

# MESURE DE LA VITESSE

# PAR TUBE PITOT

Notre autre idée cette année est de mesurer la vitesse de la Fusex via un tube de Pitot.


# PAR EFFET VENTURI

Cependant, nous avons aussi décidé, pour augmenter la difficulté, de mesurer la vitesse par effet Venturi.

# COMPARAISON

Grace aux mesures obtenues, nous pourrons comparer les deux systèmes (efficacité, précision, difficulté de réalisation). Ces résultats seront utiles pour les projets futurs du club.

Illustration 7: Exemple de tube de pitot (à titre illustratif)

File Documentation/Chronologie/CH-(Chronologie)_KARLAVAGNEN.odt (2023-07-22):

Chronologie de Karlavagnen

H- | Action | Lieu | Matériel | Qui?
Toujours | Lire et porter la chronologie | -- | Chronologie | Etienne
1j | Rassemblement du matériel | Zone travail club | Chronologie, tournevis, piles, jack, dispositif de télémesure, scotch | Tous
1j | Vérification minuterie principale: la trappe s'ouvre après 17s | Zone travail club | Tournevis | Alexandre, Damien
1j | Dépliage parachute | Zone travail club | Parachute | Geoffroy, Dimitri
3h | Récupération matériel | Zone travail club | Chronologie, tournevis, piles, jack, scotch | Tous
2h50 | Vérification minuterie principale: la trappe s'ouvre après 17s | Zone travail club | Tournevis | Damien, Alexandre
2h45 | Vérification tensionomètre: allumage, données valides | Zone travail club | Yeux, mains | Dimitri, Clément L
2h40 | Vérification caméra: allumage, enregistrement exploitable | Zone travail club | Yeux, mains | Clément B, Geoffroy
2h35 | Vérification expérience de l'école d'ingénieur: allumage | Zone travail club | Yeux, mains | Damien
2h35 | Vérification expérience de l'école d'ingénieur: localisation | Zone travail club | Yeux, mains, dispositif de télémesure | Etienne
2h30 | Dévissage de l’ogive pour changement des piles Formatage des cartes SD | Zone travail club | Tournevis, piles, scotch, ordinateur | Clément B, Etienne
2h | Repliage parachute | Zone travail club | Parachute | Damien, Alexandre et Clément
1h45 | Verrouillage de la trappe | Zone travail club | Mains | Damien, Clément L
1h20 | Transport zone tente | Camion militaire | Tournevis, jack, chronologie, fusée, scotch, dispositif de télémesure | Tous
45m | Transport zone rampe | Camion militaire | Tournevis, jack, scotch chronologie, fusée | Tous
40m | Mettre la fusée en rampe | Rampe de lancement | Fusex | Alexandre, Dimitri
35m | Fixage du fil jack sur la rampe | Rampe de lancement | Fil jack | Geoffroy
| Fixage du fil jack sur la fusée | Rampe de lancement | Fil jack | Clément B
33m | Enlever la vitre de protection du panneau de contrôle principal | Rampe de lancement | Mains | Geoffroy
32m | →Allumage du séquenceur principal: Vérification : - Diode bleue allumée - Diode blanche allumée - Diode rouge allumée ⚠️ Aucune diode ne clignote !! →Activation de l’expérience du tensionomètre: Vérification diode verte allumé | Rampe de lancement | Tournevis | Clément L Damien
26m | Remettre la vitre de protection du panneau de contrôle principal en place | Rampe de lancement | Mains | Geoffroy
25m | Allumage caméra : - enlever le dôme, - allumer la caméra - remettre le dôme | Rampe de lancement | Mains | Clément B
24m | Enlever la vitre de protection du panneau de contrôle secondaire : | Rampe de lancement | Mains | Clément L
20m | →Activation de l'expérience Pitot et Venturi : Vérification diode orange allumée | Rampe de lancement | Mains | Dimitri
17m | Demander autorisation émission 2,4 Ghz | Rampe de lancement | | Etienne
14m | →Activation de l'expérience de l'école d'ingénieur : Vérification que la connexion est bien établie entre l'antenne et le dispositif de télémesure →Activation du ventilateur pour la caméra: on peut voir s'il fonctionne dans le dôme | Rampe de lancement | Tournevis, dispositif de télémesure | Dimitri Clément B
12m | Remettre la vitre de protection du panneau de contrôle secondaire en place | Rampe de lancement | Mains | Clément L
11m | Mettre du scotch sur le panneau de contrôle principal en haut et en bas | Rampe de lancement | Mains, ciseaux, scotch | Damien
11m | Mettre du scotch sur le panneau de contrôle secondaire en haut et en bas | Rampe de lancement | Mains, ciseaux, scotch | Alexandre L
10m | Faire monter la rampe et l'orienter dans le bon angle | Rampe de lancement | Manette de contrôle de la rampe | Gars du CNES
8m | Retour en zone pupitre | -- | -- | Tous
6m | Mise en place du propulseur | Rampe de lancement | Propulseur | Pyro-techniciens
10s | Compte à rebours | Tente | Voix | Tous
- | Lancement | Pupitre de mise à feu | Mains | Alexandre

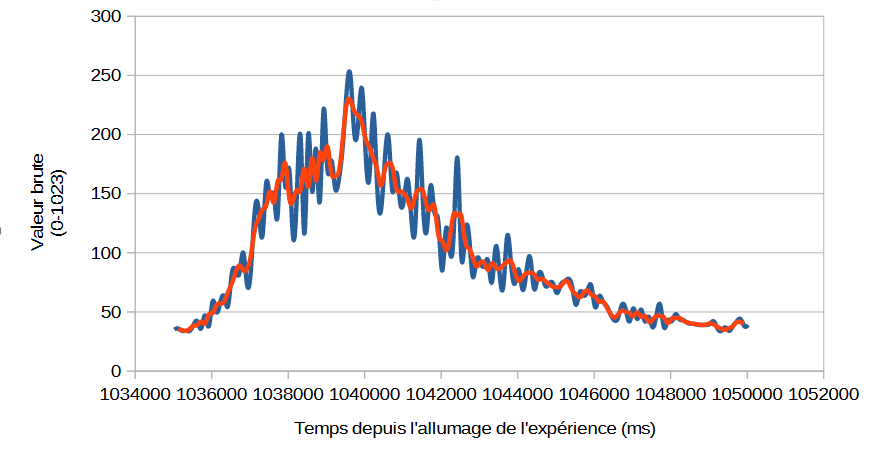
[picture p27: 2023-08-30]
Documentation/RapportDeProjet/img/Venturi.png

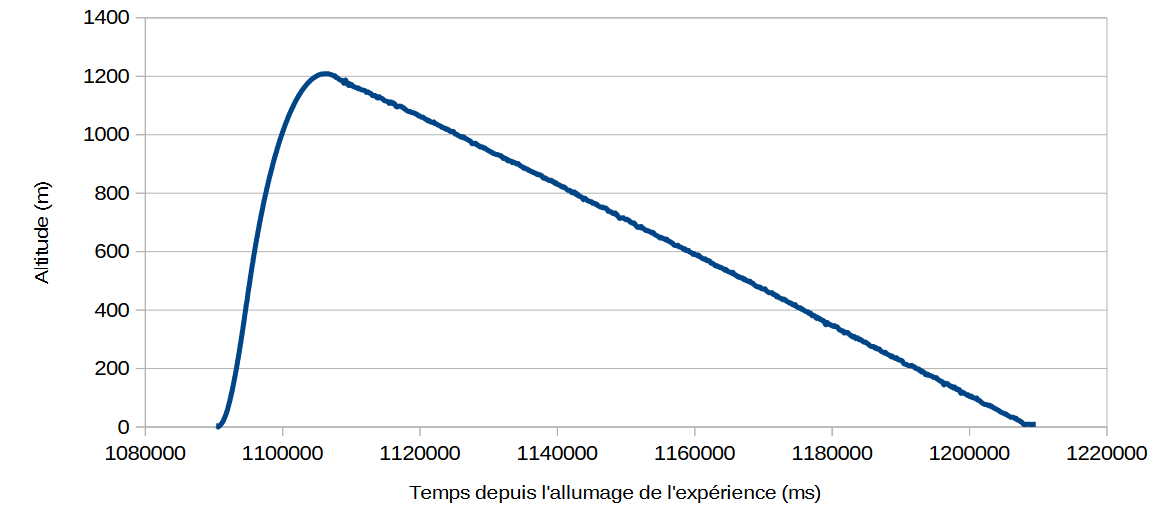
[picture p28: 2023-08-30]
Documentation/RapportDeProjet/img/Altitude.png

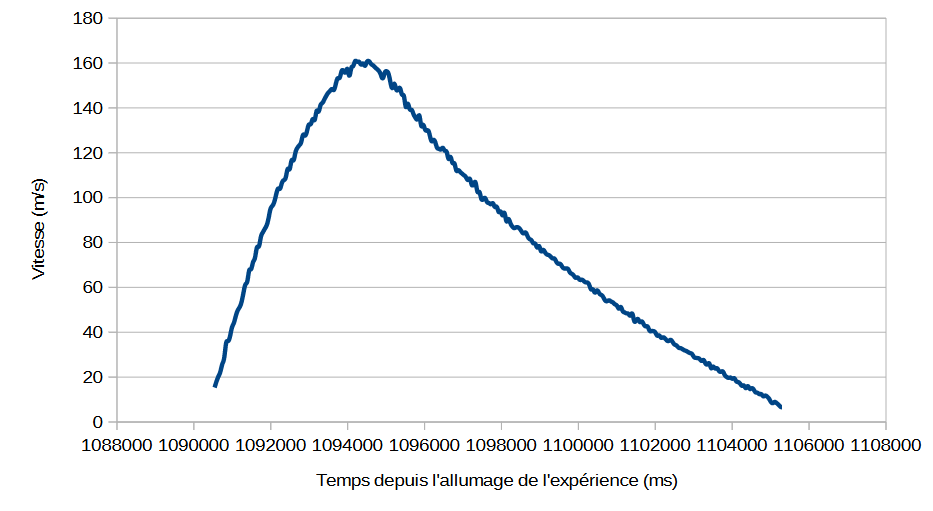
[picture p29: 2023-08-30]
Documentation/RapportDeProjet/img/Vitesse.png

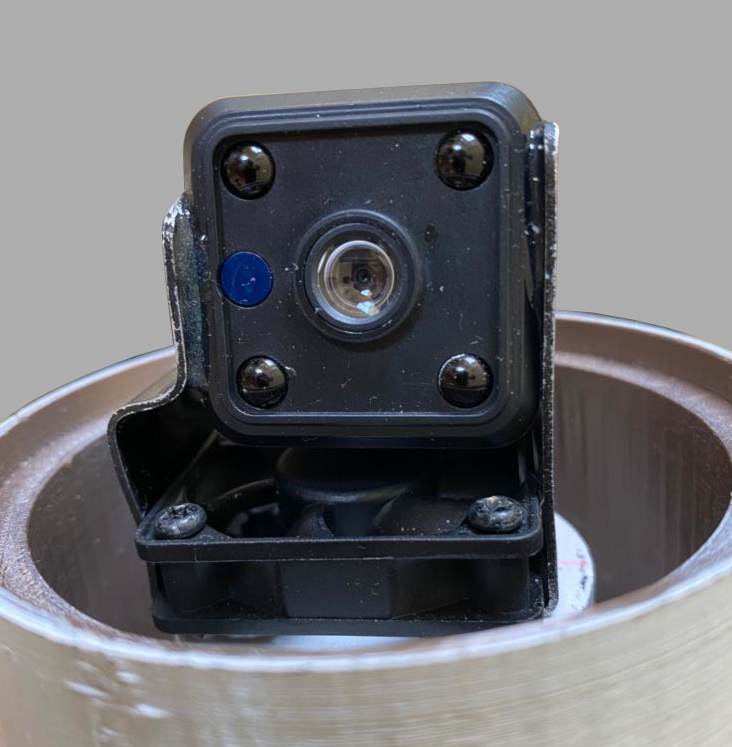
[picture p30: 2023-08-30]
Documentation/RapportDeProjet/img/CameraIRL.png

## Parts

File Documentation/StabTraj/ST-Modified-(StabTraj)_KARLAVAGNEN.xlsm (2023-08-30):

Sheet: Trajecto
 |  | TRAJECTO
 |  | Trajectographie de fusée
 |  | Remplir les cases jaunes
 |  | Fusée
 | Nom | Karlvagnen
 | Club | AcelSpace
 | Masse totale | 9.415 kg
 | Propulseur | Barasinga (Pro54-5G C)
 |  | Traînée Aérdynamique
 | Surface Réf. | 0.008854 m²
 | Cx | 0.85
 |  | Rampe de Lancement
 | Longueur | 4 m
 | Élévation | 80 °
 | Altitude | 0 m
 |  | DescenteSousParachute |  |  |  | 2023-07-27 | Temps | Altitude z | Portée x | Vitesse | Accélération | Efforts
 |  | Fusée | 0 satellite |  | Sortie de Rampe |  |  |  |  | 25.0 m/s
 | Masse | 8.382 kg | 1 kg |  | Vit max & Acc max |  |  |  |  | 173.0755398 m/s | 85.23185386 m/s²
 | Dépotage | N/A |  |  | Largage du satellite |  | 3.5 s | 374.9164085 m | 84.47883198 m | 170.3858745 m/s |  | 1778.2 N
 | Ouverture para | 16.5 s | 3.5 s |  | Culmination, Apogée |  | 15.6 s | 1224.087869 m | 445.7352571 m | 25.05558476 m/s
 | Surface para | 1.99 m² | 0.1 m² |  | Ouverture parachute fusée |  | 16.5 s | 1220.416947 m | 468.1596117 m | 26.18328787 m/s |  | 835.6 N
 | Cx parachute | 1 | 1 |  | Impact balistique |  | 33.2 s | ~0 m | 794.5330433 m | 116.4 m/s |  | 56755.14228 J
 | Vitesse du vent | 5 m/s | 5 m/s
 | Vitesse descente | 8.2 m/s | 12.7 m/s
 | Durée descente | 148.5865443 s | 29.62463382 s |  |  |  | Pour localiser la fusée
 | Durée du vol | 165.0865443 s | 33.12463382 s |  | Couleur fuselage/coiffe |  | Brun/Orange…
 | Déport latéral | ±742.9327216 m | ±148.1231691 m |  | Couleur parachute fusée |  | Rouge… |  |  |  |  |  | fichier initial
 |  |  |  |  | Couleur parachute satellite |  | Jaune |  |  |  |  |  | propu OK
 | Commentaire libre : |  |  |  |  |  |  |  |  |  |  |  | v3.4.2
Calcul de la surface d'un parachute |  |  |  |  | Résultats détaillés |  | Temps | Altitude z | Portée x | Vitesse | Accélération | Angle
 |  |  |  |  |  |  | s | m | m | m/s | m/s² | °
 |  |  |  |  | Décollage |  | 0 | 0 | 0 | 0 | - | 80
 |  |  |  |  | Sortie de Rampe |  | 0.33 | 3.78 | 0.67 | 25.0 | 80.0 | 80.0
 | Longeur du bord |  |  |  | Vit max & Acc max |  | - | - | - | 173.0755398 | 85.2 | -
 | 500 mm |  |  |  | Fin de Propulsion |  | 3.6 | 391.3582978 | 88.52932409 | 168.1834103 | 24.6 | 76.1
 | Largeur du coté |  |  |  | Culmination, Apogée |  | 15.6 | 1224.087869 | 445.7352571 | 25.05558476 | 9.8 | 0.7
 | 500 mm |  |  |  | Impact balistique |  | 33.2 | ~0 | 794.5330433 | 116.3707352 | 2.6 | -83.7
 | Surface para |  |  |  | Ouverture parachute fusée |  | 16.5 | 1220.416947 | 468.1596117 | 26.18328787 | 9.7 | -18.9
 | 1.25 m² |  |  |  | Impact fusée sous para. |  | 165.0865443 | ~0 | -275 | 1211 | 8.213509186 | 9.8 | -
 |  |  |  |  | Largage du satellite |  | 3.5 | 374.9164085 | 84.47883198 | 170.3858745 | 18.8 | 76.2
 |  |  |  |  | Impact du satellite |  | 33.12463382 | ~0 | -64 | 233 | 12.65556262 | 9.8 | -
 | Rayon exterieur
 | 800 mm
 | Rayon intérieur
 | 75 mm
 | Surface para
 | 1.99 m²
 | Vitesse de descente sous parachute :
 | Textes pour les listes déroulantes et graphiques : |  |  |  | N/A | Délais dépotage
 |  |  |  |  | -9.0 s | -9
 | 0 satellite |  |  |  | -7.0 s | -7
 | 1 satellite |  |  |  | -5.0 s | -5
 | Phase ascendante |  |  |  | -3.0 s | -3
 | Descente balistique |  |  |  | 0.0 s | -0
 | Fusée sous parachute |  |  |  | autre
 | Trajectoire (x z)
 | Portée x [m]
 | Temps [s]
 | Altitude z / Temps | 16.5 s
 | T_para =
 | Données pour les graphiques : | xz max
 |  | 1224.087869
 | xz max
 | 1224.087869 | z para
 |  | 1220.416947
 | x para | 610.2084734
 | 468.1596117 | 0
 | 468.1596117 | 61.02084734
 | 468.1596117 | 0
 | 498.6700354 | 61.02084734
 | 468.1596117 | 0
 | 437.6491881 | z para
 | 468.1596117 | 1220.416947 |  | 1 | vertical
 | t para | 610.2084734 |  | 1 | horizontal
 | 16.5 | 0 |  |  | flèches
 | 90.8 | 35.69561377 |  | 1s | 3.32
 | 165.1 | 0 |  | t/T | 0.90
 | 163.8 | 13.53882555 |  | z/Z | 1.00
 | 165.1 | 0
 | 160.4
 | 165.1 | z sat
 |  | 0
 | x sat | 0
 | 0 | 0
 | 0 | 0
 | 0 | 0
 | 0 | 0
 | 0 | 0
 | 0 | z sat
 | 0 | 0
 | t sat | 0
 | 0.0 | 0
 | 0.0 | 0
 | 0.0 | 0 |  | t/T | 0.89
 | 0.0 | 0 |  | z/Z | 1.00
 | 0.0 | 0
 | 0.0
 | 0.0 | z | x
 |  | 610.2084734 | 117.0399029
 | t | 612.0439344 | 678.2671146
 | 4.125
 | 24.4 | x_triomphe | Arc de triomphe |  | Arc de triomphe
 |  | 0 | 445.7352571 |  | 445.7352571
 | z_triomphe | 23 | 468.7352571 |  | 422.7352571
 | #N/A | 23 | 468.7352571 |  | 422.7352571
 | #N/A | 0 | 445.7352571 |  | 445.7352571
 | #N/A | 23 | 468.7352571 |  | 422.7352571
 | #N/A | 23 | 468.7352571 |  | 422.7352571
 | #N/A | 8 | 453.7352571 |  | 437.7352571
 | #N/A | 8 | 453.7352571 |  | 437.7352571
 | #N/A | 23 | 468.7352571 |  | 422.7352571
 | #N/A | 8 | 453.7352571 |  | 437.7352571
 | #N/A | 7.6 | 453.3352571 |  | 438.1352571
 | #N/A | 6.8 | 452.5352571 |  | 438.9352571
 | #N/A | 6 | 451.7352571 |  | 439.7352571
 | #N/A | 5 | 450.7352571 |  | 440.7352571
 | #N/A | 3.8 | 449.5352571 |  | 441.9352571
 | #N/A | 0 | 445.7352571 |  | 445.7352571
 | #N/A
 | #N/A | x_Eiffel | Tour Eiffel |  | Tour Eiffel
 |  | 0 | 445.7352571 |  | 445.7352571
 | z_Eiffel | 0 | 445.7352571 |  | 445.7352571
 | 324 | 10 | 455.7352571 |  | 435.7352571
 | 300 | 0 | 445.7352571 |  | 445.7352571
 | 280 | 10 | 455.7352571 |  | 435.7352571
 | 280 | 13 | 458.7352571 |  | 432.7352571
 | 280 | 17 | 462.7352571 |  | 428.7352571
 | 200 | 20 | 465.7352571 |  | 425.7352571
 | 160 | 25 | 470.7352571 |  | 420.7352571
 | 115 | 30 | 475.7352571 |  | 415.7352571
 | 90 | 36 | 481.7352571 |  | 409.7352571
 | 57 | 48 | 493.7352571 |  | 397.7352571
 | 40 | 62 | 507.7352571 |  | 383.7352571
 | 20 | 37 | 482.7352571 |  | 408.7352571
 | 0.5 | 30 | 475.7352571 |  | 415.7352571
 | 0.5 | 15 | 460.7352571 |  | 430.7352571
 | 15 | 0 | 445.7352571 |  | 445.7352571
 | 30 | 0 | 445.7352571 |  | 445.7352571
 | 37 | 17 | 462.7352571 |  | 428.7352571
 | 67 | 11 | 456.7352571 |  | 434.7352571
 | 67 | 0 | 445.7352571 |  | 445.7352571
 | 100
 | 100

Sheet: Propu
Moteur sélectionné | Ligne
Barasinga (Pro54-5G C) | 279 | I_total | 2058.4 N.s | ISP | 203.1206673 s | MpropuPlein | 1.685 kg | m_poudre | 1.033 kg | MpropuVide | 0.652 kg | XpropuPlein | 250 mm | XpropuVide | 240 mm | Longueur | 488 mm | Diamètre | 54 mm | Type | Fusex | Combustion | 0.0 s | Dépotage | 0
Temps (en s) | 0 | 0.05 | 0.5 | 1 | 1.5 | 2 | 2.5 | 2.97 | 3.2 | 3.47 | 3.59 | 3.59 | 3.59 | 3.59 | 3.59 | 3.59 | 3.59 | 3.59 | 3.59 | 3.59 | 3.59 | 3.59 | 3.59 | 1000
Poussée (en N) | 0 | 893 | 798 | 739 | 659 | 586 | 513 | 417 | 225 | 67 | 0 | 0 | 0 | 0 | 0 | 0 | 0 | 0 | 0 | 0 | 0 | 0 | 0 | 0
H2O
H2O 1.5L 300g 6bar | 26 | I_total | 9.8 N.s | ISP | 3.3 s | MpropuPlein | 0.3 kg | M_éjecté | 0.3 kg | M_burnout | 0 kg | XpropuPlein | 60 mm | XpropuVide | 150 mm | Longueur | 300 mm | Diamètre | 90 mm | Type | H2O
Temps (en s) | 0 | 0.001 | 0.02 | 0.038 | 0.04 | 0.04 | 0.04 | 0.04 | 0.04 | 0.04 | 0.04 | 0.04 | 0.04 | 0.04 | 0.04 | 0.04 | 0.04 | 0.04 | 0.04 | 0.04 | 0.04 | 0.04 | 0.04 | 1000
Poussée (en N) | 0 | 310 | 250 | 212 | 0 | 0 | 0 | 0 | 0 | 0 | 0 | 0 | 0 | 0 | 0 | 0 | 0 | 0 | 0 | 0 | 0 | 0 | 0 | 0
I_total_i (en N.s) | 0.2 | 5.3 | 4.2 | 0.2 | 0 | 0 | 0 | 0 | 0 | 0 | 0 | 0 | 0 | 0 | 0 | 0 | 0 | 0 | 0 | 0 | 0 | 0 | 0
H2O 1.5L 450g 6bar | 31 | I_total | 13.8 N.s | ISP | 3.1 s | MpropuPlein | 0.45 kg | M_éjecté | 0.45 kg | M_burnout | 0 kg | XpropuPlein | 90 mm | XpropuVide | 150 mm | Longueur | 300 mm | Diamètre | 90 mm | Type | H2O
Temps (en s) | 0 | 0.001 | 0.02 | 0.04 | 0.061 | 0.062 | 0.062 | 0.062 | 0.062 | 0.062 | 0.062 | 0.062 | 0.062 | 0.062 | 0.062 | 0.062 | 0.062 | 0.062 | 0.062 | 0.062 | 0.062 | 0.062 | 0.062 | 1000
Poussée (en N) | 0 | 310 | 245 | 200 | 167 | 0 | 0 | 0 | 0 | 0 | 0 | 0 | 0 | 0 | 0 | 0 | 0 | 0 | 0 | 0 | 0 | 0 | 0 | 0
I_total_i (en N.s) | 0.2 | 5.3 | 4.5 | 3.9 | 0.1 | 0 | 0 | 0 | 0 | 0 | 0 | 0 | 0 | 0 | 0 | 0 | 0 | 0 | 0 | 0 | 0 | 0 | 0
H2O 1.5L 600g 6bar | 36 | I_total | 17.1 N.s | ISP | 2.9 s | MpropuPlein | 0.6 kg | M_éjecté | 0.6 kg | M_burnout | 0 kg | XpropuPlein | 120 mm | XpropuVide | 150 mm | Longueur | 300 mm | Diamètre | 90 mm | Type | H2O
Temps (en s) | 0 | 0.001 | 0.02 | 0.04 | 0.06 | 0.08 | 0.088 | 0.089 | 0.089 | 0.089 | 0.089 | 0.089 | 0.089 | 0.089 | 0.089 | 0.089 | 0.089 | 0.089 | 0.089 | 0.089 | 0.089 | 0.089 | 0.089 | 1000
Poussée (en N) | 0 | 310 | 240 | 190 | 157 | 133 | 125 | 0 | 0 | 0 | 0 | 0 | 0 | 0 | 0 | 0 | 0 | 0 | 0 | 0 | 0 | 0 | 0 | 0
I_total_i (en N.s) | 0.2 | 5.2 | 4.3 | 3.5 | 2.9 | 1 | 0.1 | 0 | 0 | 0 | 0 | 0 | 0 | 0 | 0 | 0 | 0 | 0 | 0 | 0 | 0 | 0 | 0
H2O 1.5L 750g 6bar | 41 | I_total | 19.4 N.s | ISP | 2.6 s | MpropuPlein | 0.75 kg | M_éjecté | 0.75 kg | M_burnout | 0 kg | XpropuPlein | 150 mm | XpropuVide | 150 mm | Longueur | 300 mm | Diamètre | 90 mm | Type | H2O
Temps (en s) | 0 | 0.001 | 0.02 | 0.04 | 0.06 | 0.08 | 0.1 | 0.123 | 0.124 | 0.124 | 0.124 | 0.124 | 0.124 | 0.124 | 0.124 | 0.124 | 0.124 | 0.124 | 0.124 | 0.124 | 0.124 | 0.124 | 0.124 | 1000
Poussée (en N) | 0 | 310 | 230 | 175 | 140 | 118 | 100 | 85 | 0 | 0 | 0 | 0 | 0 | 0 | 0 | 0 | 0 | 0 | 0 | 0 | 0 | 0 | 0 | 0
I_total_i (en N.s) | 0.2 | 5.1 | 4 | 3.1 | 2.6 | 2.2 | 2.1 | 0.0425 | 0 | 0 | 0 | 0 | 0 | 0 | 0 | 0 | 0 | 0 | 0 | 0 | 0 | 0 | 0
H2O 2.0L 400g 6bar | 46 | I_total | 12.9 N.s | ISP | 3.3 s | MpropuPlein | 0.5 kg | M_éjecté | 0.4 kg | M_burnout | 0.1 kg | XpropuPlein | 60 mm | XpropuVide | 150 mm | Longueur | 300 mm | Diamètre | 98 mm | Type | H2O
Temps (en s) | 0 | 0.001 | 0.02 | 0.04 | 0.05 | 0.051 | 0.051 | 0.051 | 0.051 | 0.051 | 0.051 | 0.051 | 0.051 | 0.051 | 0.051 | 0.051 | 0.051 | 0.051 | 0.051 | 0.051 | 0.051 | 0.051 | 0.051 | 1000
Poussée (en N) | 0 | 310 | 264 | 230 | 213 | 0 | 0 | 0 | 0 | 0 | 0 | 0 | 0 | 0 | 0 | 0 | 0 | 0 | 0 | 0 | 0 | 0 | 0 | 0
I_total_i (en N.s) | 0.2 | 5.5 | 4.9 | 2.2 | 0.1 | 0 | 0 | 0 | 0 | 0 | 0 | 0 | 0 | 0 | 0 | 0 | 0 | 0 | 0 | 0 | 0 | 0 | 0
H2O 2.0L 600g 6bar | 51 | I_total | 18.1 N.s | ISP | 3.1 s | MpropuPlein | 0.7 kg | M_éjecté | 0.6 kg | M_burnout | 0.1 kg | XpropuPlein | 90 mm | XpropuVide | 150 mm | Longueur | 300 mm | Diamètre | 98 mm | Type | H2O
Temps (en s) | 0 | 0.001 | 0.02 | 0.04 | 0.06 | 0.08 | 0.081 | 0.081 | 0.081 | 0.081 | 0.081 | 0.081 | 0.081 | 0.081 | 0.081 | 0.081 | 0.081 | 0.081 | 0.081 | 0.081 | 0.081 | 0.081 | 0.081 | 1000
Poussée (en N) | 0 | 310 | 260 | 220 | 190 | 167 | 0 | 0 | 0 | 0 | 0 | 0 | 0 | 0 | 0 | 0 | 0 | 0 | 0 | 0 | 0 | 0 | 0 | 0
I_total_i (en N.s) | 0.2 | 5.4 | 4.8 | 4.1 | 3.6 | 0.1 | 0 | 0 | 0 | 0 | 0 | 0 | 0 | 0 | 0 | 0 | 0 | 0 | 0 | 0 | 0 | 0 | 0
H2O 2.0L 800g 6bar | 56 | I_total | 22.6 N.s | ISP | 2.9 s | MpropuPlein | 0.9 kg | M_éjecté | 0.8 kg | M_burnout | 0.1 kg | XpropuPlein | 120 mm | XpropuVide | 150 mm | Longueur | 300 mm | Diamètre | 98 mm | Type | H2O
Temps (en s) | 0 | 0.001 | 0.02 | 0.04 | 0.06 | 0.08 | 0.1 | 0.117 | 0.118 | 0.118 | 0.118 | 0.118 | 0.118 | 0.118 | 0.118 | 0.118 | 0.118 | 0.118 | 0.118 | 0.118 | 0.118 | 0.118 | 0.118 | 1000
Poussée (en N) | 0 | 310 | 250 | 210 | 180 | 156 | 140 | 125 | 0 | 0 | 0 | 0 | 0 | 0 | 0 | 0 | 0 | 0 | 0 | 0 | 0 | 0 | 0 | 0
I_total_i (en N.s) | 0.2 | 5.3 | 4.6 | 3.9 | 3.4 | 3 | 2.3 | 0.1 | 0 | 0 | 0 | 0 | 0 | 0 | 0 | 0 | 0 | 0 | 0 | 0 | 0 | 0 | 0
H2O 2.0L 1000g 6bar | 61 | I_total | 25.9 N.s | ISP | 2.6 s | MpropuPlein | 1.1 kg | M_éjecté | 1 kg | M_burnout | 0.1 kg | XpropuPlein | 150 mm | XpropuVide | 150 mm | Longueur | 300 mm | Diamètre | 98 mm | Type | H2O
Temps (en s) | 0 | 0.001 | 0.02 | 0.04 | 0.06 | 0.08 | 0.1 | 0.12 | 0.14 | 0.164 | 0.165 | 0.165 | 0.165 | 0.165 | 0.165 | 0.165 | 0.165 | 0.165 | 0.165 | 0.165 | 0.165 | 0.165 | 0.165 | 1000
Poussée (en N) | 0 | 310 | 245 | 200 | 165 | 143 | 124 | 108 | 97 | 85 | 0 | 0 | 0 | 0 | 0 | 0 | 0 | 0 | 0 | 0 | 0 | 0 | 0 | 0
I_total_i (en N.s) | 0.2 | 5.3 | 4.5 | 3.6 | 3.1 | 2.7 | 2.3 | 2 | 2.2 | 0.0425 | 0 | 0 | 0 | 0 | 0 | 0 | 0 | 0 | 0 | 0 | 0 | 0 | 0
µ-propu
µ-propu A8-3 | 67 | I_total | 2.6 N.s | ISP | 54.02650357 s | MpropuPlein | 0.015 kg | M_éjecté | 0.005 kg | M_burnout | 0.01 kg | XpropuPlein | 30 mm | XpropuVide | 30 mm | Longueur | 70 mm | Diamètre | 15 mm | Type | Micro | Combustion | 0.32 s | Dépotage | 3
Temps (en s) | 0 | 0.2 | 0.3 | 0.4 | 0.5 | 0.55 | 0.6 | 0.6 | 0.6 | 0.6 | 0.6 | 0.6 | 0.6 | 0.6 | 0.6 | 0.6 | 0.6 | 0.6 | 0.6 | 0.6 | 0.6 | 0.6 | 0.6 | 1000
Poussée (en N) | 0 | 9 | 4.5 | 4 | 4 | 3 | 0 | 0 | 0 | 0 | 0 | 0 | 0 | 0 | 0 | 0 | 0 | 0 | 0 | 0 | 0 | 0 | 0 | 0
I_total_i (en N.s) | 0.9 | 0.7 | 0.4 | 0.4 | 0.2 | 0.1 | 0 | 0 | 0 | 0 | 0 | 0 | 0 | 0 | 0 | 0 | 0 | 0 | 0 | 0 | 0 | 0 | 0
µ-propu B4-4 | 72 | I_total | 5.2 N.s | ISP | 89.19469929 s | MpropuPlein | 0.02 kg | M_éjecté | 0.006 kg | M_burnout | 0.014 kg | XpropuPlein | 30 mm | XpropuVide | 30 mm | Longueur | 70 mm | Diamètre | 15 mm | Type | Micro | Combustion | 1.20 s | Dépotage | 4
Temps (en s) | 0 | 0.2 | 0.3 | 0.55 | 1.05 | 1.15 | 1.15 | 1.15 | 1.15 | 1.15 | 1.15 | 1.15 | 1.15 | 1.15 | 1.15 | 1.15 | 1.15 | 1.15 | 1.15 | 1.15 | 1.15 | 1.15 | 1.15 | 1000
Poussée (en N) | 0 | 10 | 6 | 4 | 4 | 0 | 0 | 0 | 0 | 0 | 0 | 0 | 0 | 0 | 0 | 0 | 0 | 0 | 0 | 0 | 0 | 0 | 0 | 0
I_total_i (en N.s) | 1 | 0.8 | 1.2 | 2 | 0.2 | 0 | 0 | 0 | 0 | 0 | 0 | 0 | 0 | 0 | 0 | 0 | 0 | 0 | 0 | 0 | 0 | 0 | 0
µ-propu C6-3 | 77 | I_total | 10.3 N.s | ISP | 80.45165843 s | MpropuPlein | 0.024 kg | M_éjecté | 0.013 kg | M_burnout | 0.011 kg | XpropuPlein | 30 mm | XpropuVide | 30 mm | Longueur | 70 mm | Diamètre | 15 mm | Type | Micro | Combustion | 1.70 s | Dépotage | 3
Temps (en s) | 0 | 0.2 | 0.3 | 0.6 | 0.8 | 2 | 2.1 | 2.1 | 2.1 | 2.1 | 2.1 | 2.1 | 2.1 | 2.1 | 2.1 | 2.1 | 2.1 | 2.1 | 2.1 | 2.1 | 2.1 | 2.1 | 2.1 | 1000
Poussée (en N) | 0 | 11 | 7 | 4 | 4.6 | 4.6 | 0 | 0 | 0 | 0 | 0 | 0 | 0 | 0 | 0 | 0 | 0 | 0 | 0 | 0 | 0 | 0 | 0 | 0
I_total_i (en N.s) | 1.1 | 0.9 | 1.6 | 0.9 | 5.5 | 0.2 | 0 | 0 | 0 | 0 | 0 | 0 | 0 | 0 | 0 | 0 | 0 | 0 | 0 | 0 | 0 | 0 | 0
µ-propu C6-3 x2 | 82 | I_total | 20.5 N.s | ISP | 80.45165843 s | MpropuPlein | 0.048 kg | M_éjecté | 0.026 kg | M_burnout | 0.022 kg | XpropuPlein | 30 mm | XpropuVide | 30 mm | Longueur | 70 mm | Diamètre | 30 mm | Type | Micro | Combustion | 1.70 s | Dépotage | 3
Temps (en s) | 0 | 0.2 | 0.3 | 0.6 | 0.8 | 2 | 2.1 | 2.1 | 2.1 | 2.1 | 2.1 | 2.1 | 2.1 | 2.1 | 2.1 | 2.1 | 2.1 | 2.1 | 2.1 | 2.1 | 2.1 | 2.1 | 2.1 | 1000
Poussée (en N) | 0 | 22 | 14 | 8 | 9.2 | 9.2 | 0 | 0 | 0 | 0 | 0 | 0 | 0 | 0 | 0 | 0 | 0 | 0 | 0 | 0 | 0 | 0 | 0 | 0
I_total_i (en N.s) | 2.2 | 1.8 | 3.3 | 1.7 | 11 | 0.5 | 0 | 0 | 0 | 0 | 0 | 0 | 0 | 0 | 0 | 0 | 0 | 0 | 0 | 0 | 0 | 0 | 0
µ-propu C6-3 x3 | 87 | I_total | 30.8 N.s | ISP | 80.45165843 s | MpropuPlein | 0.072 kg | M_éjecté | 0.039 kg | M_burnout | 0.033 kg | XpropuPlein | 30 mm | XpropuVide | 30 mm | Longueur | 70 mm | Diamètre | 40 mm | Type | Micro | Combustion | 1.70 s | Dépotage | 3
Temps (en s) | 0 | 0.2 | 0.3 | 0.6 | 0.8 | 2 | 2.1 | 2.1 | 2.1 | 2.1 | 2.1 | 2.1 | 2.1 | 2.1 | 2.1 | 2.1 | 2.1 | 2.1 | 2.1 | 2.1 | 2.1 | 2.1 | 2.1 | 1000
Poussée (en N) | 0 | 33 | 21 | 12 | 13.8 | 13.8 | 0 | 0 | 0 | 0 | 0 | 0 | 0 | 0 | 0 | 0 | 0 | 0 | 0 | 0 | 0 | 0 | 0 | 0
I_total_i (en N.s) | 3.3 | 2.7 | 5 | 2.6 | 16.6 | 0.7 | 0 | 0 | 0 | 0 | 0 | 0 | 0 | 0 | 0 | 0 | 0 | 0 | 0 | 0 | 0 | 0 | 0
Klima D9-7 | 92 | I_total | 20.0 N.s | ISP | 118.3058874 s | MpropuPlein | 0.0282 kg | M_éjecté | 0.0172 kg | M_burnout | 0.011 kg | XpropuPlein | 30 mm | XpropuVide | 30 mm | Longueur | 70 mm | Diamètre | 18 mm | Type | MiniN | Combustion | 2.10 s | Dépotage | 7
Temps (en s) | 0 | 0.04 | 0.116 | 0.213 | 0.286 | 0.329 | 0.369 | 0.42 | 0.495 | 0.597 | 1.711 | 1.826 | 1.917 | 1.975 | 2.206 | 2.242 | 2.5 | 2.5 | 2.5 | 2.5 | 2.5 | 2.5 | 2.5 | 1000
Poussée (en N) | 0 | 2.111 | 9.685 | 25 | 15.738 | 12.472 | 10.67 | 9.713 | 9.178 | 8.896 | 8.925 | 8.699 | 8.052 | 6.954 | 1.07 | 0 | 0 | 0 | 0 | 0 | 0 | 0 | 0 | 0
I_total_i (en N.s) | 0.04222 | 0.4 | 1.7 | 1.5 | 0.6 | 0.5 | 0.5 | 0.7 | 0.9 | 9.9 | 1 | 0.8 | 0.4 | 0.9 | 0.01926 | 0 | 0 | 0 | 0 | 0 | 0 | 0 | 0
Klima D9-7 x2 | 97 | I_total | 39.9 N.s | ISP | 118.3058874 s | MpropuPlein | 0.0564 kg | M_éjecté | 0.0344 kg | M_burnout | 0.022 kg | XpropuPlein | 30 mm | XpropuVide | 30 mm | Longueur | 70 mm | Diamètre | 30 mm | Type | MiniN | Combustion | 2.10 s | Dépotage | 7
Temps (en s) | 0 | 0.04 | 0.116 | 0.213 | 0.286 | 0.329 | 0.369 | 0.42 | 0.495 | 0.597 | 1.711 | 1.826 | 1.917 | 1.975 | 2.206 | 2.242 | 2.5 | 2.5 | 2.5 | 2.5 | 2.5 | 2.5 | 2.5 | 1000
Poussée (en N) | 0 | 4.222 | 19.37 | 50 | 31.476 | 24.944 | 21.34 | 19.426 | 18.356 | 17.792 | 17.85 | 17.398 | 16.104 | 13.908 | 2.14 | 0 | 0 | 0 | 0 | 0 | 0 | 0 | 0 | 0
I_total_i (en N.s) | 0.1 | 0.9 | 3.4 | 3 | 1.2 | 0.9 | 1 | 1.4 | 1.8 | 19.9 | 2 | 1.5 | 0.9 | 1.9 | 0.03852 | 0 | 0 | 0 | 0 | 0 | 0 | 0 | 0
Klima D9-7 x3 | 102 | I_total | 59.9 N.s | ISP | 118.3058874 s | MpropuPlein | 0.0846 kg | M_éjecté | 0.0516 kg | M_burnout | 0.033 kg | XpropuPlein | 30 mm | XpropuVide | 30 mm | Longueur | 70 mm | Diamètre | 40 mm | Type | MiniN | Combustion | 2.10 s | Dépotage | 7
Temps (en s) | 0 | 0.04 | 0.116 | 0.213 | 0.286 | 0.329 | 0.369 | 0.42 | 0.495 | 0.597 | 1.711 | 1.826 | 1.917 | 1.975 | 2.206 | 2.242 | 2.5 | 2.5 | 2.5 | 2.5 | 2.5 | 2.5 | 2.5 | 1000
Poussée (en N) | 0 | 6.333 | 29.055 | 75 | 47.214 | 37.416 | 32.01 | 29.139 | 27.534 | 26.688 | 26.775 | 26.097 | 24.156 | 20.862 | 3.21 | 0 | 0 | 0 | 0 | 0 | 0 | 0 | 0 | 0
I_total_i (en N.s) | 0.1 | 1.3 | 5 | 4.5 | 1.8 | 1.4 | 1.6 | 2.1 | 2.8 | 29.8 | 3 | 2.3 | 1.3 | 2.8 | 0.1 | 0 | 0 | 0 | 0 | 0 | 0 | 0 | 0
MINIF PRO24-1G
p24-1G 24E22 | 108 | I_total | 24.3 N.s | ISP | 154.6223178 s | MpropuPlein | 0.052 kg | M_éjecté | 0.016 kg | M_burnout | 0.036 kg | XpropuPlein | 35.0 mm | XpropuVide | 35.0 mm | Longueur | 69 mm | Diamètre | 24 mm | Type | MiniR | Combustion | 1.00 s | Dépotage | 13
Temps (en s) | 0 | 0.008 | 0.026 | 0.038 | 0.067 | 0.101 | 0.33 | 0.528 | 0.716 | 0.841 | 0.912 | 0.987 | 1.016 | 1.065 | 1.087 | 2 | 2 | 2 | 2 | 2 | 2 | 2 | 2 | 1000
Poussée (en N) | 0 | 18.292 | 30 | 30.792 | 18.708 | 21.875 | 26.083 | 28.042 | 27.875 | 23.542 | 17.833 | 7 | 3.333 | 1.083 | 0 | 0 | 0 | 0 | 0 | 0 | 0 | 0 | 0 | 0
I_total_i (en N.s) | 0.1 | 0.4 | 0.4 | 0.7 | 0.7 | 5.5 | 5.4 | 5.3 | 3.2 | 1.5 | 0.9 | 0.1 | 0.1 | 0.011913 | 0 | 0 | 0 | 0 | 0 | 0 | 0 | 0 | 0
p24-1G 25E75 (Rufina) | 113 | I_total | 24.5 N.s | ISP | 121.7717014 s | MpropuPlein | 0.0565 kg | M_éjecté | 0.0205 kg | M_burnout | 0.036 kg | XpropuPlein | 35.0 mm | XpropuVide | 35.0 mm | Longueur | 69 mm | Diamètre | 24 mm | Type | MiniRN | Combustion | 0.33 s | Dépotage | 17
Temps (en s) | 0 | 0.009 | 0.012 | 0.023 | 0.027 | 0.047 | 0.092 | 0.118 | 0.141 | 0.192 | 0.222 | 0.25 | 0.26 | 0.281 | 0.287 | 0.306 | 0.314 | 0.326 | 0.329 | 0.5 | 1 | 2 | 2 | 1000
Poussée (en N) | 0 | 84.213 | 95.099 | 77.08 | 68.697 | 73.452 | 81.835 | 83.837 | 86.465 | 86.966 | 85.339 | 80.083 | 78.332 | 82.961 | 78.206 | 24.776 | 14.14 | 8.509 | 0 | 0 | 0 | 0 | 0 | 0
I_total_i (en N.s) | 0.4 | 0.3 | 0.9 | 0.3 | 1.4 | 3.5 | 2.2 | 2 | 4.4 | 2.6 | 2.3 | 0.8 | 1.7 | 0.5 | 1 | 0.2 | 0.1 | 0.0127635 | 0 | 0 | 0 | 0 | 0
p24-1G 26E31 | 118 | I_total | 26.1 N.s | ISP | 166.1823554 s | MpropuPlein | 0.052 kg | M_éjecté | 0.016 kg | M_burnout | 0.036 kg | XpropuPlein | 35.0 mm | XpropuVide | 35.0 mm | Longueur | 69 mm | Diamètre | 24 mm | Type | MiniR | Combustion | 0.85 s | Dépotage | 15
Temps (en s) | 0 | 0.02 | 0.027 | 0.049 | 0.113 | 0.193 | 0.282 | 0.5 | 0.727 | 0.771 | 0.807 | 0.84 | 0.87 | 1 | 1 | 1 | 1 | 1 | 1 | 1 | 1 | 1 | 2 | 1000
Poussée (en N) | 0 | 43.824 | 39.964 | 26.781 | 32.601 | 34.739 | 35.808 | 34.442 | 29.276 | 22.743 | 9.561 | 3.563 | 0 | 0 | 0 | 0 | 0 | 0 | 0 | 0 | 0 | 0 | 0 | 0
I_total_i (en N.s) | 0.4 | 0.3 | 0.7 | 1.9 | 2.7 | 3.1 | 7.7 | 7.2 | 1.1 | 0.6 | 0.2 | 0.1 | 0 | 0 | 0 | 0 | 0 | 0 | 0 | 0 | 0 | 0 | 0
MINIF PRO24-2G
p24-2G 50E51 | 123 | I_total | 49.8 N.s | ISP | 231 s | MpropuPlein | 0.073 kg | M_éjecté | 0.028 kg | M_burnout | 0.045 kg | XpropuPlein | 50.0 mm | XpropuVide | 50.0 mm | Longueur | 101 mm | Diamètre | 24 mm | Type | Mini | Combustion | 1.00 s | Dépotage | 13
Temps (en s) | 0 | 0.001 | 0.027 | 0.051 | 0.06 | 0.092 | 0.119 | 0.17 | 0.3 | 0.462 | 0.569 | 0.675 | 0.778 | 0.846 | 0.917 | 1.009 | 1.032 | 1.045 | 2 | 2 | 2 | 2 | 2 | 1000
Poussée (en N) | 0 | 5.145 | 67.976 | 53.807 | 52.88 | 55.916 | 57.94 | 59.711 | 61.145 | 58.952 | 55.578 | 52.205 | 46.386 | 38.12 | 20.325 | 3.542 | 1.602 | 0 | 0 | 0 | 0 | 0 | 0 | 0
I_total_i (en N.s) | 0.0025725 | 1 | 1.5 | 0.5 | 1.7 | 1.5 | 3 | 7.9 | 9.7 | 6.1 | 5.7 | 5.1 | 2.9 | 2.1 | 1.1 | 0.1 | 0.010413 | 0 | 0 | 0 | 0 | 0 | 0
p24-1G 53E70 | 128 | I_total | 52.8 N.s | ISP | 239 s | MpropuPlein | 0.073 kg | M_éjecté | 0.029 kg | M_burnout | 0.044 kg | XpropuPlein | 50.0 mm | XpropuVide | 50.0 mm | Longueur | 101 mm | Diamètre | 24 mm | Type | Mini | Combustion | 0.77 s | Dépotage | 14
Temps (en s) | 0 | 0.001 | 0.013 | 0.023 | 0.052 | 0.1 | 0.379 | 0.641 | 0.665 | 0.706 | 0.744 | 0.787 | 0.816 | 1 | 1 | 1 | 1 | 1 | 1 | 1 | 1 | 2 | 2 | 1000
Poussée (en N) | 0 | 8.303 | 85.68 | 96.149 | 78.821 | 83.634 | 77.858 | 62.575 | 55.716 | 23.947 | 9.146 | 2.768 | 0 | 0 | 0 | 0 | 0 | 0 | 0 | 0 | 0 | 0 | 0 | 0
I_total_i (en N.s) | 0.0041515 | 0.6 | 0.9 | 2.5 | 3.9 | 22.5 | 18.4 | 1.4 | 1.6 | 0.6 | 0.3 | 0.040136 | 0 | 0 | 0 | 0 | 0 | 0 | 0 | 0 | 0 | 0 | 0
MINIF PRO29-1G
p29-1G 41F36 | 133 | I_total | 41.8 N.s | ISP | 121.8435998 s | MpropuPlein | 0.104 kg | M_éjecté | 0.035 kg | M_burnout | 0.069 kg | XpropuPlein | 49 mm | XpropuVide | 49 mm | Longueur | 98 mm | Diamètre | 29 mm | Type | MiniR | Combustion | 1.07 s | Dépotage | 11
Temps (en s) | 0 | 0.01 | 0.02 | 0.03 | 0.04 | 0.06 | 0.07 | 0.08 | 0.1 | 0.2 | 0.3 | 0.4 | 0.5 | 0.6 | 0.7 | 0.8 | 0.85 | 0.92 | 0.95 | 0.99 | 1.05 | 1.05 | 2 | 1000
Poussée (en N) | 0 | 12 | 46 | 75 | 79 | 77 | 62 | 32 | 35 | 38 | 39 | 41 | 43 | 43 | 43 | 43 | 47 | 54 | 32 | 8 | 0 | 0 | 0 | 0
I_total_i (en N.s) | 0.1 | 0.3 | 0.6 | 0.8 | 1.6 | 0.7 | 0.5 | 0.7 | 3.6 | 3.9 | 4 | 4.2 | 4.3 | 4.3 | 4.3 | 2.2 | 3.5 | 1.3 | 0.8 | 0.2 | 0 | 0 | 0
p29-1G 51F36 | 138 | I_total | 52.6 N.s | ISP | 167.4471203 s | MpropuPlein | 0.101 kg | M_éjecté | 0.032 kg | M_burnout | 0.069 kg | XpropuPlein | 49 mm | XpropuVide | 49 mm | Longueur | 98 mm | Diamètre | 29 mm | Type | MiniRN | Combustion | 1.80 s | Dépotage | 12
Temps (en s) | 0 | 0.01 | 0.03 | 0.04 | 0.05 | 0.06 | 0.07 | 0.08 | 0.09 | 0.1 | 0.2 | 0.3 | 0.4 | 0.5 | 0.7 | 0.8 | 0.9 | 1 | 1.1 | 1.24 | 1.3 | 1.5 | 2 | 1000
Poussée (en N) | 0 | 12 | 41 | 42 | 42 | 40 | 34 | 34 | 35 | 36 | 40 | 42 | 43 | 43 | 43 | 42 | 41 | 40 | 38 | 37 | 12 | 0 | 0 | 0
I_total_i (en N.s) | 0.1 | 0.5 | 0.4 | 0.4 | 0.4 | 0.4 | 0.3 | 0.3 | 0.4 | 3.8 | 4.1 | 4.2 | 4.3 | 8.6 | 4.2 | 4.2 | 4 | 3.9 | 5.2 | 1.5 | 1.2 | 0 | 0
p29-1G 55F29 | 143 | I_total | 54.1 N.s | ISP | 146.6968576 s | MpropuPlein | 0.1058 kg | M_éjecté | 0.0376 kg | M_burnout | 0.0682 kg | XpropuPlein | 49 mm | XpropuVide | 49 mm | Longueur | 98 mm | Diamètre | 29 mm | Type | MiniR | Combustion | 1.90 s | Dépotage | 12
Temps (en s) | 0 | 0.025 | 0.05 | 0.075 | 0.1 | 0.15 | 0.175 | 0.2 | 0.3 | 0.4 | 0.5 | 0.6 | 0.7 | 0.8 | 0.9 | 1.1 | 1.2 | 1.6 | 1.7 | 1.8 | 1.9 | 1.9999 | 2 | 1000
Poussée (en N) | 0 | 15.26 | 26.38 | 21.48 | 24.02 | 28.11 | 28.69 | 29.18 | 31.49 | 32.56 | 32.83 | 32.65 | 32.38 | 32.25 | 31.80 | 30.56 | 30.07 | 26.38 | 24.87 | 18.46 | 7.52 | 1.38 | 0 | 0
I_total_i (en N.s) | 0.2 | 0.5 | 0.6 | 0.6 | 1.3 | 0.7 | 0.7 | 3 | 3.2 | 3.3 | 3.3 | 3.3 | 3.2 | 3.2 | 6.2 | 3 | 11.3 | 2.6 | 2.2 | 1.3 | 0.4 | 6.894743524e-05 | 0
p29-1G 56F31 | 148 | I_total | 55.6 N.s | ISP | 177.0817151 s | MpropuPlein | 0.102 kg | M_éjecté | 0.032 kg | M_burnout | 0.07 kg | XpropuPlein | 49 mm | XpropuVide | 49 mm | Longueur | 98 mm | Diamètre | 29 mm | Type | MiniRN | Combustion | 0.45 s | Dépotage | 12
Temps (en s) | 0 | 0.001 | 0.023 | 0.05 | 0.059 | 0.095 | 0.212 | 0.344 | 1.567 | 1.631 | 1.663 | 1.785 | 1.828 | 2 | 2 | 2 | 2 | 2 | 2 | 2 | 2 | 2 | 2 | 1000
Poussée (en N) | 0 | 3.483 | 64.053 | 31.347 | 28.459 | 32.027 | 36.189 | 37.549 | 26.165 | 26.93 | 25.316 | 3.653 | 0 | 0 | 0 | 0 | 0 | 0 | 0 | 0 | 0 | 0 | 0 | 0
I_total_i (en N.s) | 0.0017415 | 0.7 | 1.3 | 0.3 | 1.1 | 4 | 4.9 | 39 | 1.7 | 0.8 | 1.8 | 0.1 | 0 | 0 | 0 | 0 | 0 | 0 | 0 | 0 | 0 | 0 | 0
p29-1G 56F120 | 153 | I_total | 55.7 N.s | ISP | 180.8432981 s | MpropuPlein | 0.1062 kg | M_éjecté | 0.0314 kg | M_burnout | 0.0748 kg | XpropuPlein | 49 mm | XpropuVide | 49 mm | Longueur | 98 mm | Diamètre | 29 mm | Type | MiniRN | Combustion | 0.45 s | Dépotage | 14
Temps (en s) | 0 | 0.013 | 0.017 | 0.04 | 0.125 | 0.179 | 0.222 | 0.289 | 0.354 | 0.394 | 0.406 | 0.416 | 0.423 | 0.431 | 0.447 | 0.453 | 0.455 | 0.455 | 0.455 | 0.455 | 0.455 | 0.455 | 2 | 1000
Poussée (en N) | 0 | 79.242 | 90.427 | 101.422 | 127.583 | 136.114 | 139.905 | 143.507 | 138.578 | 125.498 | 123.602 | 125.118 | 130.047 | 120.569 | 25.592 | 8.72 | 0 | 0 | 0 | 0 | 0 | 0 | 0 | 0
I_total_i (en N.s) | 0.5 | 0.3 | 2.2 | 9.7 | 7.1 | 5.9 | 9.5 | 9.2 | 5.3 | 1.5 | 1.2 | 0.9 | 1 | 1.2 | 0.1 | 0.00872 | 0 | 0 | 0 | 0 | 0 | 0 | 0
p29-1G 57F59 | 158 | I_total | 57.2 N.s | ISP | 188.0569531 s | MpropuPlein | 0.099 kg | M_éjecté | 0.031 kg | M_burnout | 0.068 kg | XpropuPlein | 49 mm | XpropuVide | 49 mm | Longueur | 98 mm | Diamètre | 29 mm | Type | MiniRN | Combustion | 0.96 s | Dépotage | 12
Temps (en s) | 0 | 0.01 | 0.02 | 0.03 | 0.04 | 0.07 | 0.1 | 0.2 | 0.3 | 0.4 | 0.5 | 0.6 | 0.7 | 0.87 | 0.9 | 0.97 | 0.97 | 0.97 | 0.97 | 0.97 | 0.97 | 0.97 | 2 | 1000
Poussée (en N) | 0 | 16 | 62 | 67 | 71 | 58 | 63 | 67 | 69 | 67 | 65 | 63 | 61 | 60 | 23 | 0 | 0 | 0 | 0 | 0 | 0 | 0 | 0 | 0
I_total_i (en N.s) | 0.1 | 0.4 | 0.6 | 0.7 | 1.9 | 1.8 | 6.5 | 6.8 | 6.8 | 6.6 | 6.4 | 6.2 | 10.3 | 1.2 | 0.8 | 0 | 0 | 0 | 0 | 0 | 0 | 0 | 0
MINIF PRO24-3G
p24-3G 60F50 | 163 | I_total | 59.7 N.s | ISP | 190.7792477 s | MpropuPlein | 0.0939 kg | M_éjecté | 0.0319 kg | M_burnout | 0.062 kg | XpropuPlein | 66.5 mm | XpropuVide | 66.5 mm | Longueur | 133 mm | Diamètre | 24 mm | Type | MiniR | Combustion | 1.20 s | Dépotage | 13
Temps (en s) | 0 | 0.015 | 0.022 | 0.064 | 0.118 | 0.342 | 0.536 | 0.743 | 0.884 | 0.976 | 1.096 | 1.246 | 1.298 | 2 | 2 | 2 | 2 | 2 | 2 | 2 | 2 | 2 | 2 | 1000
Poussée (en N) | 0 | 64.982 | 69.516 | 55.537 | 62.81 | 62.149 | 59.41 | 53.837 | 46.942 | 40.047 | 12.562 | 2.078 | 0 | 0 | 0 | 0 | 0 | 0 | 0 | 0 | 0 | 0 | 0 | 0
I_total_i (en N.s) | 0.5 | 0.5 | 2.6 | 3.2 | 14 | 11.8 | 11.7 | 7.1 | 4 | 3.2 | 1.1 | 0.1 | 0 | 0 | 0 | 0 | 0 | 0 | 0 | 0 | 0 | 0 | 0
p24-3G 68F79 | 168 | I_total | 68.4 N.s | ISP | 134.048073 s | MpropuPlein | 0.1075 kg | M_éjecté | 0.052 kg | M_burnout | 0.0555 kg | XpropuPlein | 66.5 mm | XpropuVide | 66.5 mm | Longueur | 133 mm | Diamètre | 24 mm | Type | MiniR | Combustion | 0.86 s | Dépotage | 13
Temps (en s) | 0 | 0.005 | 0.013 | 0.022 | 0.043 | 0.119 | 0.198 | 0.267 | 0.343 | 0.404 | 0.498 | 0.555 | 0.622 | 0.663 | 0.704 | 0.729 | 0.747 | 0.768 | 0.821 | 0.852 | 0.892 | 1 | 2 | 1000
Poussée (en N) | 0 | 60 | 89.007 | 96.291 | 81.722 | 85.563 | 87.947 | 89.272 | 89.934 | 90.861 | 91.523 | 89.669 | 83.974 | 80.53 | 78.94 | 74.172 | 66.887 | 53.775 | 18.543 | 7.815 | 2.119 | 0 | 0 | 0
I_total_i (en N.s) | 0.1 | 0.6 | 0.8 | 1.9 | 6.4 | 6.9 | 6.1 | 6.8 | 5.5 | 8.6 | 5.2 | 5.8 | 3.4 | 3.3 | 1.9 | 1.3 | 1.3 | 1.9 | 0.4 | 0.2 | 0.1 | 0 | 0
p24-3G 68F240 | 173 | I_total | 68.0 N.s | ISP | 181.8954586 s | MpropuPlein | 0.0918 kg | M_éjecté | 0.0381 kg | M_burnout | 0.0537 kg | XpropuPlein | 66.5 mm | XpropuVide | 66.5 mm | Longueur | 133 mm | Diamètre | 24 mm | Type | MiniR | Combustion | 0.33 s | Dépotage | 15
Temps (en s) | 0 | 0.004 | 0.007 | 0.01 | 0.022 | 0.028 | 0.041 | 0.058 | 0.077 | 0.089 | 0.097 | 0.119 | 0.147 | 0.177 | 0.207 | 0.253 | 0.259 | 0.272 | 0.28 | 0.286 | 0.294 | 0.328 | 2 | 1000
Poussée (en N) | 0 | 100.53 | 197.49 | 222.03 | 241.43 | 237.86 | 239.45 | 252.51 | 263.98 | 275.46 | 271.50 | 278.63 | 281.40 | 272.30 | 258.44 | 218.47 | 188.79 | 74.80 | 31.27 | 15.83 | 8.71 | 0.00 | 0 | 0
I_total_i (en N.s) | 0.2 | 0.4 | 0.6 | 2.8 | 1.4 | 3.1 | 4.2 | 4.9 | 3.2 | 2.2 | 6.1 | 7.8 | 8.3 | 8 | 11 | 1.2 | 1.7 | 0.4 | 0.1 | 0.1 | 0.1 | 0 | 0
p24-3G 73F30 | 178 | I_total | 73.6 N.s | ISP | 156.866193 s | MpropuPlein | 0.1022 kg | M_éjecté | 0.0478 kg | M_burnout | 0.0544 kg | XpropuPlein | 66.5 mm | XpropuVide | 66.5 mm | Longueur | 133 mm | Diamètre | 24 mm | Type | MiniR | Combustion | 2.36 s | Dépotage | 6
Temps (en s) | 0 | 0.014 | 0.056 | 0.092 | 0.16 | 0.232 | 0.363 | 0.499 | 0.655 | 0.843 | 1.216 | 1.368 | 1.54 | 1.675 | 1.861 | 2.013 | 2.159 | 2.302 | 2.462 | 2.598 | 2.598 | 2.598 | 2.598 | 1000
Poussée (en N) | 0 | 54.22 | 43.46 | 50.19 | 54.06 | 48.36 | 45.75 | 43.14 | 40.29 | 37.84 | 32.61 | 30.32 | 26.36 | 23.51 | 19.08 | 14.56 | 10.05 | 4.83 | 1.50 | 0 | 0 | 0 | 0 | 0
I_total_i (en N.s) | 0.4 | 2.1 | 1.7 | 3.5 | 3.7 | 6.2 | 6 | 6.5 | 7.3 | 13.1 | 4.8 | 4.9 | 3.4 | 4 | 2.6 | 1.8 | 1.1 | 0.5 | 0.1 | 0 | 0 | 0 | 0
p24-3G 74F85 | 183 | I_total | 73.2 N.s | ISP | 177.5872967 s | MpropuPlein | 0.096 kg | M_éjecté | 0.042 kg | M_burnout | 0.054 kg | XpropuPlein | 66.5 mm | XpropuVide | 66.5 mm | Longueur | 133 mm | Diamètre | 24 mm | Type | MiniR | Combustion | 0.87 s | Dépotage | 15
Temps (en s) | 0 | 0.01 | 0.023 | 0.04 | 0.118 | 0.283 | 0.51 | 0.688 | 0.787 | 0.852 | 0.873 | 0.873 | 0.873 | 0.873 | 0.873 | 0.873 | 0.873 | 0.873 | 0.873 | 0.873 | 0.873 | 0.873 | 2 | 1000
Poussée (en N) | 0 | 76.07 | 100.19 | 92.42 | 100.88 | 102.40 | 96.44 | 87.44 | 25.91 | 7.21 | 0 | 0 | 0 | 0 | 0 | 0 | 0 | 0 | 0 | 0 | 0 | 0 | 0 | 0
I_total_i (en N.s) | 0.4 | 1.1 | 1.6 | 7.5 | 16.8 | 22.6 | 16.4 | 5.6 | 1.1 | 0.1 | 0 | 0 | 0 | 0 | 0 | 0 | 0 | 0 | 0 | 0 | 0 | 0 | 0
p24-3G 75F51 | 188 | I_total | 75.3 N.s | ISP | 232.4603342 s | MpropuPlein | 0.095 kg | M_éjecté | 0.033 kg | M_burnout | 0.062 kg | XpropuPlein | 66.5 mm | XpropuVide | 66.5 mm | Longueur | 133 mm | Diamètre | 24 mm | Type | MiniR | Combustion | 1.50 s | Dépotage | 12
Temps (en s) | 0 | 0.02 | 0.031 | 0.062 | 0.117 | 1.211 | 1.376 | 1.456 | 1.532 | 1.577 | 2 | 2 | 2 | 2 | 2 | 2 | 2 | 2 | 2 | 2 | 2 | 2 | 2 | 1000
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

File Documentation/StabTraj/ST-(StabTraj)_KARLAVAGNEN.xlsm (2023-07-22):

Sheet: Trajecto
 |  | TRAJECTO
 |  | Trajectographie de fusée
 |  | Remplir les cases jaunes
 |  | Fusée
 | Nom | Karlvagnen
 | Club | AcelSpace
 | Masse totale | 9.415 kg
 | Propulseur | Barasinga (Pro54-5G C)
 |  | Traînée Aérdynamique
 | Surface Réf. | 0.008854 m²
 | Cx | 0.6
 |  | Rampe de Lancement
 | Longueur | 4 m
 | Élévation | 80 °
 | Altitude | 0 m
 |  | DescenteSousParachute |  |  |  | 2023-07-19 | Temps | Altitude z | Portée x | Vitesse | Accélération | Efforts
 |  | Fusée | 0 satellite |  | Sortie de Rampe |  |  |  |  | 25.0 m/s
 | Masse | 8.382 kg | 1 kg |  | Vit max & Acc max |  |  |  |  | 179.2876292 m/s | 85.23237003 m/s²
 | Dépotage | N/A |  |  | Largage du satellite |  | 3.5 s | 382.3749004 m | 86.09030508 m | 177.5474998 m/s |  | 1930.8 N
 | Ouverture para | 8 s | 3.5 s |  | Culmination, Apogée |  | 16.9 s | 1390.423049 m | 523.6979948 m | 28.21611251 m/s
 | Surface para | 1.25 m² | 0.1 m² |  | Ouverture parachute fusée |  | 8.0 s | 977.7584382 m | 254.4642656 m | 103.3610633 m/s |  | 8179.6 N
 | Cx parachute | 1 | 1 |  | Impact balistique |  | 35.3 s | ~0 m | 953.1802661 m | 131.2 m/s |  | 72155.46531 J
 | Vitesse du vent | 5 m/s | 5 m/s
 | Vitesse descente | 10.4 m/s | 12.7 m/s
 | Durée descente | 94.34769486 s | 30.21397877 s |  |  |  | Pour localiser la fusée |  |  |  |  |  |  | Ouverture parachute fusée précoce.
 | Durée du vol | 102.3476949 s | 33.71397877 s |  | Couleur fuselage/coiffe |  | Brun/Orange… |  |  |  |  |  |  | Attention, aux efforts sur le parachute lors de l'ouverture !
 | Déport latéral | ±471.7384743 m | ±151.0698939 m |  | Couleur parachute fusée |  | Rouge… |  |  |  |  |  | fichier initial
 |  |  |  |  | Couleur parachute satellite |  | Jaune |  |  |  |  |  | propu OK
 | Commentaire libre : |  |  |  |  |  |  |  |  |  |  |  | v3.4.2
Calcul de la surface d'un parachute |  |  |  |  | Résultats détaillés |  | Temps | Altitude z | Portée x | Vitesse | Accélération | Angle
 |  |  |  |  |  |  | s | m | m | m/s | m/s² | °
 |  |  |  |  | Décollage |  | 0 | 0 | 0 | 0 | - | 80
 |  |  |  |  | Sortie de Rampe |  | 0.33 | 3.78 | 0.67 | 25.0 | 80.1 | 80.0
 | Longeur du bord |  |  |  | Vit max & Acc max |  | - | - | - | 179.2876292 | 85.2 | -
 | 500 mm |  |  |  | Fin de Propulsion |  | 3.6 | 399.5329012 | 90.30221144 | 175.6980191 | 21.2 | 76.2
 | Largeur du coté |  |  |  | Culmination, Apogée |  | 16.9 | 1390.423049 | 523.6979948 | 28.21611251 | 9.8 | 0.1
 | 500 mm |  |  |  | Impact balistique |  | 35.3 | ~0 | 953.1802661 | 131.2126738 | 3.3 | -82.8
 | Surface para |  |  |  | Ouverture parachute fusée |  | 8.0 | 977.7584382 | 254.4642656 | 103.3610633 | 13.5 | 71.0
 | 1.25 m² |  |  |  | Impact fusée sous para. |  | 102.3476949 | ~0 | -217 | 726 | 10.3633527 | 9.8 | -
 |  |  |  |  | Largage du satellite |  | 3.5 | 382.3749004 | 86.09030508 | 177.5474998 | 15.2 | 76.2
 |  |  |  |  | Impact du satellite |  | 33.71397877 | ~0 | -65 | 237 | 12.65556262 | 9.8 | -
 | Rayon exterieur
 | 800 mm
 | Rayon intérieur
 | 75 mm
 | Surface para
 | 1.99 m²
 | Vitesse de descente sous parachute :
 | Textes pour les listes déroulantes et graphiques : |  |  |  | N/A | Délais dépotage
 |  |  |  |  | -9.0 s | -9
 | 0 satellite |  |  |  | -7.0 s | -7
 | 1 satellite |  |  |  | -5.0 s | -5
 | Phase ascendante |  |  |  | -3.0 s | -3
 | Descente balistique |  |  |  | 0.0 s | -0
 | Fusée sous parachute |  |  |  | autre
 | Trajectoire (x z)
 | Portée x [m]
 | Temps [s]
 | Altitude z / Temps | 8
 | T_para =
 | Données pour les graphiques : | xz max
 |  | 1390.423049
 | xz max
 | 1390.423049 | z para
 |  | 977.7584382
 | x para | 488.8792191
 | 254.4642656 | 0
 | 254.4642656 | 48.88792191
 | 254.4642656 | 0
 | 278.9082265 | 48.88792191
 | 254.4642656 | 0
 | 230.0203046 | z para
 | 254.4642656 | 977.7584382 |  | 1 | vertical
 | t para | 488.8792191 |  | 1 | horizontal
 | 8.0 | 0 |  |  | flèches
 | 55.2 | 70.05986573 |  | 1s | 3.53
 | 102.3 | 0 |  | t/T | 0.92
 | 100.9 | 25.85227709 |  | z/Z | 1.00
 | 102.3 | 0
 | 97.3
 | 102.3 | z sat
 |  | FALSE
 | x sat | FALSE
 | FALSE | FALSE
 | FALSE | FALSE
 | FALSE | FALSE
 | FALSE | FALSE
 | FALSE | FALSE
 | FALSE | z sat
 | FALSE | FALSE
 | t sat | 0
 | FALSE | FALSE
 | 0.0 | FALSE
 | FALSE | FALSE |  | t/T | 0.90
 | FALSE | FALSE |  | z/Z | 1.05
 | FALSE | FALSE
 | FALSE
 | FALSE | z | x
 |  | 488.8792191 | 63.61606639
 | t | 695.2115246 | 810.019509
 | 2
 | 26.1 | x_triomphe | Arc de triomphe |  | Arc de triomphe
 |  | 0 | 523.6979948 |  | 523.6979948
 | z_triomphe | 23 | 546.6979948 |  | 500.6979948
 | #N/A | 23 | 546.6979948 |  | 500.6979948
 | #N/A | 0 | 523.6979948 |  | 523.6979948
 | #N/A | 23 | 546.6979948 |  | 500.6979948
 | #N/A | 23 | 546.6979948 |  | 500.6979948
 | #N/A | 8 | 531.6979948 |  | 515.6979948
 | #N/A | 8 | 531.6979948 |  | 515.6979948
 | #N/A | 23 | 546.6979948 |  | 500.6979948
 | #N/A | 8 | 531.6979948 |  | 515.6979948
 | #N/A | 7.6 | 531.2979948 |  | 516.0979948
 | #N/A | 6.8 | 530.4979948 |  | 516.8979948
 | #N/A | 6 | 529.6979948 |  | 517.6979948
 | #N/A | 5 | 528.6979948 |  | 518.6979948
 | #N/A | 3.8 | 527.4979948 |  | 519.8979948
 | #N/A | 0 | 523.6979948 |  | 523.6979948
 | #N/A
 | #N/A | x_Eiffel | Tour Eiffel |  | Tour Eiffel
 |  | 0 | 523.6979948 |  | 523.6979948
 | z_Eiffel | 0 | 523.6979948 |  | 523.6979948
 | 324 | 10 | 533.6979948 |  | 513.6979948
 | 300 | 0 | 523.6979948 |  | 523.6979948
 | 280 | 10 | 533.6979948 |  | 513.6979948
 | 280 | 13 | 536.6979948 |  | 510.6979948
 | 280 | 17 | 540.6979948 |  | 506.6979948
 | 200 | 20 | 543.6979948 |  | 503.6979948
 | 160 | 25 | 548.6979948 |  | 498.6979948
 | 115 | 30 | 553.6979948 |  | 493.6979948
 | 90 | 36 | 559.6979948 |  | 487.6979948
 | 57 | 48 | 571.6979948 |  | 475.6979948
 | 40 | 62 | 585.6979948 |  | 461.6979948
 | 20 | 37 | 560.6979948 |  | 486.6979948
 | 0.5 | 30 | 553.6979948 |  | 493.6979948
 | 0.5 | 15 | 538.6979948 |  | 508.6979948
 | 15 | 0 | 523.6979948 |  | 523.6979948
 | 30 | 0 | 523.6979948 |  | 523.6979948
 | 37 | 17 | 540.6979948 |  | 506.6979948
 | 67 | 11 | 534.6979948 |  | 512.6979948
 | 67 | 0 | 523.6979948 |  | 523.6979948
 | 100
 | 100

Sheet: Propu
Moteur sélectionné | Ligne
Barasinga (Pro54-5G C) | 279 | I_total | 2058.4 N.s | ISP | 203.1206673 s | MpropuPlein | 1.685 kg | m_poudre | 1.033 kg | MpropuVide | 0.652 kg | XpropuPlein | 250 mm | XpropuVide | 240 mm | Longueur | 488 mm | Diamètre | 54 mm | Type | Fusex | Combustion | 0.0 s | Dépotage | 0
Temps (en s) | 0 | 0.05 | 0.5 | 1 | 1.5 | 2 | 2.5 | 2.97 | 3.2 | 3.47 | 3.59 | 3.59 | 3.59 | 3.59 | 3.59 | 3.59 | 3.59 | 3.59 | 3.59 | 3.59 | 3.59 | 3.59 | 3.59 | 1000
Poussée (en N) | 0 | 893 | 798 | 739 | 659 | 586 | 513 | 417 | 225 | 67 | 0 | 0 | 0 | 0 | 0 | 0 | 0 | 0 | 0 | 0 | 0 | 0 | 0 | 0
H2O
H2O 1.5L 300g 6bar | 26 | I_total | 9.8 N.s | ISP | 3.3 s | MpropuPlein | 0.3 kg | M_éjecté | 0.3 kg | M_burnout | 0 kg | XpropuPlein | 60 mm | XpropuVide | 150 mm | Longueur | 300 mm | Diamètre | 90 mm | Type | H2O
Temps (en s) | 0 | 0.001 | 0.02 | 0.038 | 0.04 | 0.04 | 0.04 | 0.04 | 0.04 | 0.04 | 0.04 | 0.04 | 0.04 | 0.04 | 0.04 | 0.04 | 0.04 | 0.04 | 0.04 | 0.04 | 0.04 | 0.04 | 0.04 | 1000
Poussée (en N) | 0 | 310 | 250 | 212 | 0 | 0 | 0 | 0 | 0 | 0 | 0 | 0 | 0 | 0 | 0 | 0 | 0 | 0 | 0 | 0 | 0 | 0 | 0 | 0
I_total_i (en N.s) | 0.2 | 5.3 | 4.2 | 0.2 | 0 | 0 | 0 | 0 | 0 | 0 | 0 | 0 | 0 | 0 | 0 | 0 | 0 | 0 | 0 | 0 | 0 | 0 | 0
H2O 1.5L 450g 6bar | 31 | I_total | 13.8 N.s | ISP | 3.1 s | MpropuPlein | 0.45 kg | M_éjecté | 0.45 kg | M_burnout | 0 kg | XpropuPlein | 90 mm | XpropuVide | 150 mm | Longueur | 300 mm | Diamètre | 90 mm | Type | H2O
Temps (en s) | 0 | 0.001 | 0.02 | 0.04 | 0.061 | 0.062 | 0.062 | 0.062 | 0.062 | 0.062 | 0.062 | 0.062 | 0.062 | 0.062 | 0.062 | 0.062 | 0.062 | 0.062 | 0.062 | 0.062 | 0.062 | 0.062 | 0.062 | 1000
Poussée (en N) | 0 | 310 | 245 | 200 | 167 | 0 | 0 | 0 | 0 | 0 | 0 | 0 | 0 | 0 | 0 | 0 | 0 | 0 | 0 | 0 | 0 | 0 | 0 | 0
I_total_i (en N.s) | 0.2 | 5.3 | 4.5 | 3.9 | 0.1 | 0 | 0 | 0 | 0 | 0 | 0 | 0 | 0 | 0 | 0 | 0 | 0 | 0 | 0 | 0 | 0 | 0 | 0
H2O 1.5L 600g 6bar | 36 | I_total | 17.1 N.s | ISP | 2.9 s | MpropuPlein | 0.6 kg | M_éjecté | 0.6 kg | M_burnout | 0 kg | XpropuPlein | 120 mm | XpropuVide | 150 mm | Longueur | 300 mm | Diamètre | 90 mm | Type | H2O
Temps (en s) | 0 | 0.001 | 0.02 | 0.04 | 0.06 | 0.08 | 0.088 | 0.089 | 0.089 | 0.089 | 0.089 | 0.089 | 0.089 | 0.089 | 0.089 | 0.089 | 0.089 | 0.089 | 0.089 | 0.089 | 0.089 | 0.089 | 0.089 | 1000
Poussée (en N) | 0 | 310 | 240 | 190 | 157 | 133 | 125 | 0 | 0 | 0 | 0 | 0 | 0 | 0 | 0 | 0 | 0 | 0 | 0 | 0 | 0 | 0 | 0 | 0
I_total_i (en N.s) | 0.2 | 5.2 | 4.3 | 3.5 | 2.9 | 1 | 0.1 | 0 | 0 | 0 | 0 | 0 | 0 | 0 | 0 | 0 | 0 | 0 | 0 | 0 | 0 | 0 | 0
H2O 1.5L 750g 6bar | 41 | I_total | 19.4 N.s | ISP | 2.6 s | MpropuPlein | 0.75 kg | M_éjecté | 0.75 kg | M_burnout | 0 kg | XpropuPlein | 150 mm | XpropuVide | 150 mm | Longueur | 300 mm | Diamètre | 90 mm | Type | H2O
Temps (en s) | 0 | 0.001 | 0.02 | 0.04 | 0.06 | 0.08 | 0.1 | 0.123 | 0.124 | 0.124 | 0.124 | 0.124 | 0.124 | 0.124 | 0.124 | 0.124 | 0.124 | 0.124 | 0.124 | 0.124 | 0.124 | 0.124 | 0.124 | 1000
Poussée (en N) | 0 | 310 | 230 | 175 | 140 | 118 | 100 | 85 | 0 | 0 | 0 | 0 | 0 | 0 | 0 | 0 | 0 | 0 | 0 | 0 | 0 | 0 | 0 | 0
I_total_i (en N.s) | 0.2 | 5.1 | 4 | 3.1 | 2.6 | 2.2 | 2.1 | 0.0425 | 0 | 0 | 0 | 0 | 0 | 0 | 0 | 0 | 0 | 0 | 0 | 0 | 0 | 0 | 0
H2O 2.0L 400g 6bar | 46 | I_total | 12.9 N.s | ISP | 3.3 s | MpropuPlein | 0.5 kg | M_éjecté | 0.4 kg | M_burnout | 0.1 kg | XpropuPlein | 60 mm | XpropuVide | 150 mm | Longueur | 300 mm | Diamètre | 98 mm | Type | H2O
Temps (en s) | 0 | 0.001 | 0.02 | 0.04 | 0.05 | 0.051 | 0.051 | 0.051 | 0.051 | 0.051 | 0.051 | 0.051 | 0.051 | 0.051 | 0.051 | 0.051 | 0.051 | 0.051 | 0.051 | 0.051 | 0.051 | 0.051 | 0.051 | 1000
Poussée (en N) | 0 | 310 | 264 | 230 | 213 | 0 | 0 | 0 | 0 | 0 | 0 | 0 | 0 | 0 | 0 | 0 | 0 | 0 | 0 | 0 | 0 | 0 | 0 | 0
I_total_i (en N.s) | 0.2 | 5.5 | 4.9 | 2.2 | 0.1 | 0 | 0 | 0 | 0 | 0 | 0 | 0 | 0 | 0 | 0 | 0 | 0 | 0 | 0 | 0 | 0 | 0 | 0
H2O 2.0L 600g 6bar | 51 | I_total | 18.1 N.s | ISP | 3.1 s | MpropuPlein | 0.7 kg | M_éjecté | 0.6 kg | M_burnout | 0.1 kg | XpropuPlein | 90 mm | XpropuVide | 150 mm | Longueur | 300 mm | Diamètre | 98 mm | Type | H2O
Temps (en s) | 0 | 0.001 | 0.02 | 0.04 | 0.06 | 0.08 | 0.081 | 0.081 | 0.081 | 0.081 | 0.081 | 0.081 | 0.081 | 0.081 | 0.081 | 0.081 | 0.081 | 0.081 | 0.081 | 0.081 | 0.081 | 0.081 | 0.081 | 1000
Poussée (en N) | 0 | 310 | 260 | 220 | 190 | 167 | 0 | 0 | 0 | 0 | 0 | 0 | 0 | 0 | 0 | 0 | 0 | 0 | 0 | 0 | 0 | 0 | 0 | 0
I_total_i (en N.s) | 0.2 | 5.4 | 4.8 | 4.1 | 3.6 | 0.1 | 0 | 0 | 0 | 0 | 0 | 0 | 0 | 0 | 0 | 0 | 0 | 0 | 0 | 0 | 0 | 0 | 0
H2O 2.0L 800g 6bar | 56 | I_total | 22.6 N.s | ISP | 2.9 s | MpropuPlein | 0.9 kg | M_éjecté | 0.8 kg | M_burnout | 0.1 kg | XpropuPlein | 120 mm | XpropuVide | 150 mm | Longueur | 300 mm | Diamètre | 98 mm | Type | H2O
Temps (en s) | 0 | 0.001 | 0.02 | 0.04 | 0.06 | 0.08 | 0.1 | 0.117 | 0.118 | 0.118 | 0.118 | 0.118 | 0.118 | 0.118 | 0.118 | 0.118 | 0.118 | 0.118 | 0.118 | 0.118 | 0.118 | 0.118 | 0.118 | 1000
Poussée (en N) | 0 | 310 | 250 | 210 | 180 | 156 | 140 | 125 | 0 | 0 | 0 | 0 | 0 | 0 | 0 | 0 | 0 | 0 | 0 | 0 | 0 | 0 | 0 | 0
I_total_i (en N.s) | 0.2 | 5.3 | 4.6 | 3.9 | 3.4 | 3 | 2.3 | 0.1 | 0 | 0 | 0 | 0 | 0 | 0 | 0 | 0 | 0 | 0 | 0 | 0 | 0 | 0 | 0
H2O 2.0L 1000g 6bar | 61 | I_total | 25.9 N.s | ISP | 2.6 s | MpropuPlein | 1.1 kg | M_éjecté | 1 kg | M_burnout | 0.1 kg | XpropuPlein | 150 mm | XpropuVide | 150 mm | Longueur | 300 mm | Diamètre | 98 mm | Type | H2O
Temps (en s) | 0 | 0.001 | 0.02 | 0.04 | 0.06 | 0.08 | 0.1 | 0.12 | 0.14 | 0.164 | 0.165 | 0.165 | 0.165 | 0.165 | 0.165 | 0.165 | 0.165 | 0.165 | 0.165 | 0.165 | 0.165 | 0.165 | 0.165 | 1000
Poussée (en N) | 0 | 310 | 245 | 200 | 165 | 143 | 124 | 108 | 97 | 85 | 0 | 0 | 0 | 0 | 0 | 0 | 0 | 0 | 0 | 0 | 0 | 0 | 0 | 0
I_total_i (en N.s) | 0.2 | 5.3 | 4.5 | 3.6 | 3.1 | 2.7 | 2.3 | 2.1 | 2.2 | 0.0425 | 0 | 0 | 0 | 0 | 0 | 0 | 0 | 0 | 0 | 0 | 0 | 0 | 0
µ-propu
µ-propu A8-3 | 67 | I_total | 2.6 N.s | ISP | 54.02650357 s | MpropuPlein | 0.015 kg | M_éjecté | 0.005 kg | M_burnout | 0.01 kg | XpropuPlein | 30 mm | XpropuVide | 30 mm | Longueur | 70 mm | Diamètre | 15 mm | Type | Micro | Combustion | 0.32 s | Dépotage | 3
Temps (en s) | 0 | 0.2 | 0.3 | 0.4 | 0.5 | 0.55 | 0.6 | 0.6 | 0.6 | 0.6 | 0.6 | 0.6 | 0.6 | 0.6 | 0.6 | 0.6 | 0.6 | 0.6 | 0.6 | 0.6 | 0.6 | 0.6 | 0.6 | 1000
Poussée (en N) | 0 | 9 | 4.5 | 4 | 4 | 3 | 0 | 0 | 0 | 0 | 0 | 0 | 0 | 0 | 0 | 0 | 0 | 0 | 0 | 0 | 0 | 0 | 0 | 0
I_total_i (en N.s) | 0.9 | 0.7 | 0.4 | 0.4 | 0.2 | 0.1 | 0 | 0 | 0 | 0 | 0 | 0 | 0 | 0 | 0 | 0 | 0 | 0 | 0 | 0 | 0 | 0 | 0
µ-propu B4-4 | 72 | I_total | 5.2 N.s | ISP | 89.19469929 s | MpropuPlein | 0.02 kg | M_éjecté | 0.006 kg | M_burnout | 0.014 kg | XpropuPlein | 30 mm | XpropuVide | 30 mm | Longueur | 70 mm | Diamètre | 15 mm | Type | Micro | Combustion | 1.20 s | Dépotage | 4
Temps (en s) | 0 | 0.2 | 0.3 | 0.55 | 1.05 | 1.15 | 1.15 | 1.15 | 1.15 | 1.15 | 1.15 | 1.15 | 1.15 | 1.15 | 1.15 | 1.15 | 1.15 | 1.15 | 1.15 | 1.15 | 1.15 | 1.15 | 1.15 | 1000
Poussée (en N) | 0 | 10 | 6 | 4 | 4 | 0 | 0 | 0 | 0 | 0 | 0 | 0 | 0 | 0 | 0 | 0 | 0 | 0 | 0 | 0 | 0 | 0 | 0 | 0
I_total_i (en N.s) | 1 | 0.8 | 1.3 | 2 | 0.2 | 0 | 0 | 0 | 0 | 0 | 0 | 0 | 0 | 0 | 0 | 0 | 0 | 0 | 0 | 0 | 0 | 0 | 0
µ-propu C6-3 | 77 | I_total | 10.3 N.s | ISP | 80.45165843 s | MpropuPlein | 0.024 kg | M_éjecté | 0.013 kg | M_burnout | 0.011 kg | XpropuPlein | 30 mm | XpropuVide | 30 mm | Longueur | 70 mm | Diamètre | 15 mm | Type | Micro | Combustion | 1.70 s | Dépotage | 3
Temps (en s) | 0 | 0.2 | 0.3 | 0.6 | 0.8 | 2 | 2.1 | 2.1 | 2.1 | 2.1 | 2.1 | 2.1 | 2.1 | 2.1 | 2.1 | 2.1 | 2.1 | 2.1 | 2.1 | 2.1 | 2.1 | 2.1 | 2.1 | 1000
Poussée (en N) | 0 | 11 | 7 | 4 | 4.6 | 4.6 | 0 | 0 | 0 | 0 | 0 | 0 | 0 | 0 | 0 | 0 | 0 | 0 | 0 | 0 | 0 | 0 | 0 | 0
I_total_i (en N.s) | 1.1 | 0.9 | 1.6 | 0.9 | 5.5 | 0.2 | 0 | 0 | 0 | 0 | 0 | 0 | 0 | 0 | 0 | 0 | 0 | 0 | 0 | 0 | 0 | 0 | 0
µ-propu C6-3 x2 | 82 | I_total | 20.5 N.s | ISP | 80.45165843 s | MpropuPlein | 0.048 kg | M_éjecté | 0.026 kg | M_burnout | 0.022 kg | XpropuPlein | 30 mm | XpropuVide | 30 mm | Longueur | 70 mm | Diamètre | 30 mm | Type | Micro | Combustion | 1.70 s | Dépotage | 3
Temps (en s) | 0 | 0.2 | 0.3 | 0.6 | 0.8 | 2 | 2.1 | 2.1 | 2.1 | 2.1 | 2.1 | 2.1 | 2.1 | 2.1 | 2.1 | 2.1 | 2.1 | 2.1 | 2.1 | 2.1 | 2.1 | 2.1 | 2.1 | 1000
Poussée (en N) | 0 | 22 | 14 | 8 | 9.2 | 9.2 | 0 | 0 | 0 | 0 | 0 | 0 | 0 | 0 | 0 | 0 | 0 | 0 | 0 | 0 | 0 | 0 | 0 | 0
I_total_i (en N.s) | 2.2 | 1.8 | 3.3 | 1.7 | 11 | 0.5 | 0 | 0 | 0 | 0 | 0 | 0 | 0 | 0 | 0 | 0 | 0 | 0 | 0 | 0 | 0 | 0 | 0
µ-propu C6-3 x3 | 87 | I_total | 30.8 N.s | ISP | 80.45165843 s | MpropuPlein | 0.072 kg | M_éjecté | 0.039 kg | M_burnout | 0.033 kg | XpropuPlein | 30 mm | XpropuVide | 30 mm | Longueur | 70 mm | Diamètre | 40 mm | Type | Micro | Combustion | 1.70 s | Dépotage | 3
Temps (en s) | 0 | 0.2 | 0.3 | 0.6 | 0.8 | 2 | 2.1 | 2.1 | 2.1 | 2.1 | 2.1 | 2.1 | 2.1 | 2.1 | 2.1 | 2.1 | 2.1 | 2.1 | 2.1 | 2.1 | 2.1 | 2.1 | 2.1 | 1000
Poussée (en N) | 0 | 33 | 21 | 12 | 13.8 | 13.8 | 0 | 0 | 0 | 0 | 0 | 0 | 0 | 0 | 0 | 0 | 0 | 0 | 0 | 0 | 0 | 0 | 0 | 0
I_total_i (en N.s) | 3.3 | 2.7 | 5 | 2.6 | 16.6 | 0.7 | 0 | 0 | 0 | 0 | 0 | 0 | 0 | 0 | 0 | 0 | 0 | 0 | 0 | 0 | 0 | 0 | 0
Klima D9-7 | 92 | I_total | 20.0 N.s | ISP | 118.3058874 s | MpropuPlein | 0.0282 kg | M_éjecté | 0.0172 kg | M_burnout | 0.011 kg | XpropuPlein | 30 mm | XpropuVide | 30 mm | Longueur | 70 mm | Diamètre | 18 mm | Type | MiniN | Combustion | 2.10 s | Dépotage | 7
Temps (en s) | 0 | 0.04 | 0.116 | 0.213 | 0.286 | 0.329 | 0.369 | 0.42 | 0.495 | 0.597 | 1.711 | 1.826 | 1.917 | 1.975 | 2.206 | 2.242 | 2.5 | 2.5 | 2.5 | 2.5 | 2.5 | 2.5 | 2.5 | 1000
Poussée (en N) | 0 | 2.111 | 9.685 | 25 | 15.738 | 12.472 | 10.67 | 9.713 | 9.178 | 8.896 | 8.925 | 8.699 | 8.052 | 6.954 | 1.07 | 0 | 0 | 0 | 0 | 0 | 0 | 0 | 0 | 0
I_total_i (en N.s) | 0.04222 | 0.4 | 1.7 | 1.5 | 0.6 | 0.5 | 0.5 | 0.7 | 0.9 | 9.9 | 1 | 0.8 | 0.4 | 0.9 | 0.01926 | 0 | 0 | 0 | 0 | 0 | 0 | 0 | 0
Klima D9-7 x2 | 97 | I_total | 39.9 N.s | ISP | 118.3058874 s | MpropuPlein | 0.0564 kg | M_éjecté | 0.0344 kg | M_burnout | 0.022 kg | XpropuPlein | 30 mm | XpropuVide | 30 mm | Longueur | 70 mm | Diamètre | 30 mm | Type | MiniN | Combustion | 2.10 s | Dépotage | 7
Temps (en s) | 0 | 0.04 | 0.116 | 0.213 | 0.286 | 0.329 | 0.369 | 0.42 | 0.495 | 0.597 | 1.711 | 1.826 | 1.917 | 1.975 | 2.206 | 2.242 | 2.5 | 2.5 | 2.5 | 2.5 | 2.5 | 2.5 | 2.5 | 1000
Poussée (en N) | 0 | 4.222 | 19.37 | 50 | 31.476 | 24.944 | 21.34 | 19.426 | 18.356 | 17.792 | 17.85 | 17.398 | 16.104 | 13.908 | 2.14 | 0 | 0 | 0 | 0 | 0 | 0 | 0 | 0 | 0
I_total_i (en N.s) | 0.1 | 0.9 | 3.4 | 3 | 1.2 | 0.9 | 1 | 1.4 | 1.8 | 19.9 | 2 | 1.5 | 0.9 | 1.9 | 0.03852 | 0 | 0 | 0 | 0 | 0 | 0 | 0 | 0
Klima D9-7 x3 | 102 | I_total | 59.9 N.s | ISP | 118.3058874 s | MpropuPlein | 0.0846 kg | M_éjecté | 0.0516 kg | M_burnout | 0.033 kg | XpropuPlein | 30 mm | XpropuVide | 30 mm | Longueur | 70 mm | Diamètre | 40 mm | Type | MiniN | Combustion | 2.10 s | Dépotage | 7
Temps (en s) | 0 | 0.04 | 0.116 | 0.213 | 0.286 | 0.329 | 0.369 | 0.42 | 0.495 | 0.597 | 1.711 | 1.826 | 1.917 | 1.975 | 2.206 | 2.242 | 2.5 | 2.5 | 2.5 | 2.5 | 2.5 | 2.5 | 2.5 | 1000
Poussée (en N) | 0 | 6.333 | 29.055 | 75 | 47.214 | 37.416 | 32.01 | 29.139 | 27.534 | 26.688 | 26.775 | 26.097 | 24.156 | 20.862 | 3.21 | 0 | 0 | 0 | 0 | 0 | 0 | 0 | 0 | 0
I_total_i (en N.s) | 0.1 | 1.3 | 5 | 4.5 | 1.8 | 1.4 | 1.6 | 2.1 | 2.8 | 29.8 | 3 | 2.3 | 1.3 | 2.8 | 0.1 | 0 | 0 | 0 | 0 | 0 | 0 | 0 | 0
MINIF PRO24-1G
p24-1G 24E22 | 108 | I_total | 24.3 N.s | ISP | 154.6223178 s | MpropuPlein | 0.052 kg | M_éjecté | 0.016 kg | M_burnout | 0.036 kg | XpropuPlein | 35.0 mm | XpropuVide | 35.0 mm | Longueur | 69 mm | Diamètre | 24 mm | Type | MiniR | Combustion | 1.00 s | Dépotage | 13
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

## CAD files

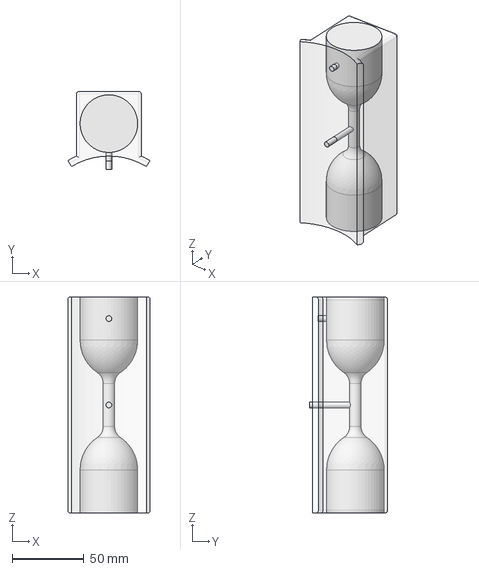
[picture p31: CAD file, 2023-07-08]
Modelisation3D/Module_Vitesse-Dimitri/venturi.FCStd
57.0 x 54.5 x 150.0 mm

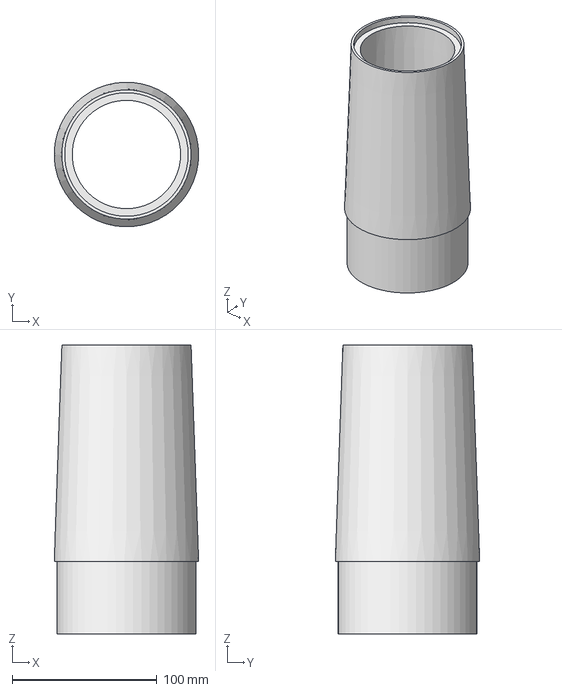
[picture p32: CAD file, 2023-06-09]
Modelisation3D/Ogive-Dimitri/Ogive.FCStd
99.9 x 100.0 x 200.0 mm

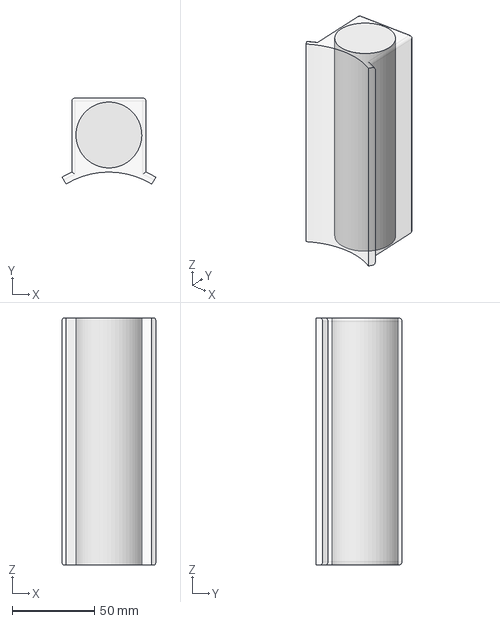
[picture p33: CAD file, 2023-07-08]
Modelisation3D/Module_Vitesse-Dimitri/bloc.FCStd
57.0 x 52.3 x 150.0 mm

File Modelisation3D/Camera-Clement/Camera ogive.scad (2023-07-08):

//corps de la fusée 
translate([300,0,0])
cylinder(h = 2000, r1 = 100, r2 = 100, center = false);
//ogive
x=350;
translate([300,0,2000]){
    for ( i = [0 : 0.01 : 10] ){
        translate([0,0,i*35]) cylinder(10,100-(i^2),100-(i^2));
}}

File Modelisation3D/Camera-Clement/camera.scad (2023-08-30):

use <../library/meca-comps/meca-comps.scad>

module bloc_camera(d_int=96) {

// //ogive (réduction du diamètre)
// difference(){
//     translate([0,0,200]) cylinder(h = 70, r1 = 50, r2 = 42.5, center = false);
//     translate([0,0,198.4]) cylinder(h = 72, r1 = 35, r2 = 27, center = false);
// }

// //ogive (dôme)
// translate([0,0,270]) 
// difference(){
//     #sphere(r = 42.5);
//     translate([0,0,-50]) cube(100,true);
//     #sphere(r = 39.5);
// }

//support caméra
// difference(){
//     translate([0,0,200]) cylinder(h = 20, r1 = 50, r2 = 30, center = false);
//     translate([0,0,202]) cylinder(h = 19.4, r1 = 35, r2 = 24.55, center = false);
// }

//batterie
// color([0.9, 0, 0]) {
//     translate([-20,0,195]) cube([51, 34, 4]);
// }

// support
translate([0, 0, -11])
color("white")
difference(){
    cylinder(h=10, d1=82, d2=81);
    translate([0,0,-1])
    cylinder(h=12,d=10);
};

// servo-moteur
color([50/255,50/255,255/255])
translate([0,-7,8.5-28])
cube([8, 19, 17],true);
// color([50/255,50/255,255/255])
// translate([23/2+10,0,17/2+5])
// rotate([0,0,90]) 
// cube([8, 19, 17],true);


// axe
translate([0, 0, -11])
color("grey")
cylinder(h=15,d=5);

// pattes support caméra
union() {
    translate([23/2,-10/2,4])
    cube([5,10,35]);
    translate([-23/2-5,-10/2,4])
    cube([5,10,35]);
    translate([-23/2-5,-10/2,4])
    cube([33,10,5]);
}

// ventilo
color([0.1,0.1,0.1]) 
translate([0,0,11]) 
cube([20,20,4],true);

// caméra
translate([0,0,15]) {
    translate([0,0,23/2])
    color("dimgrey") 
    cube(23,true);
    translate([0,23/2+1,23/2])
    color("navy")
    rotate([90,0,0])
    cylinder(h=1,d=10);
}

}

bloc_camera();

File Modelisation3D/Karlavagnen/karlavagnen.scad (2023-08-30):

/*Global*/
use <../library/elec-cartes/elec-cartes.scad>
use <../library/elec-comps/elec-comps.scad>
use <../library/meca-comps/meca-comps.scad>

/*Persos*/
use <../Ogive-Dimitri/ogive.scad>
use <../Camera-Clement/camera.scad>
use <../Tensionometre-Etienne/tensionometre.scad>
use <../Module_Vitesse-Dimitri/vitesse.scad>
use <../Minuterie-Alexandre/minuterie.scad>
use <../Mini_Ailerons-ClementL/roulis.scad>

/*Variables*/
d_ext=100;
d_int=96;
l_tube=2000;


/*Camera*/
translate([0,0,l_tube+150])
bloc_camera(d_int);

/*Ogive*/
translate([0,0,l_tube])
ogiveK(d_ext);

/*Module vitesse*/
translate([0,0,l_tube-216])
vitesse();


/*Trappe*/
translate([0,0,1000]) 
color("red") 
cylinder(h=500,d=d_int);


/*Bloc Minuterie*/
translate([0,0,500]) {
    /*Minuterie*/
    minuterie(d_int);
    /*Tensionometre*/
    scale([0.5,0.5,1]) 
    translate([-50,0,130]) 
    tensionometre();
}


for (i=[0:1:3]) {
    color("dimgrey") {
    // equerres bague de pousée
    rotate([0,0,90*i]) 
    translate([1,-33,8]) 
    rotate([90,0,0])
    equerre(20, 20, 10, 1);

    rotate([0,0,90*i]) 
    translate([-33,1,8])
    rotate([0,-90,0])
    equerre(20, 20, 10, 1);

    // equerres bague mileu
    rotate([0,0,90*i]) 
    translate([1,-33,170]) 
    rotate([90,0,0])
    equerre(20, 20, 10, 1);

    rotate([0,0,90*i]) 
    translate([-33,1,170])
    rotate([0,-90,0])
    equerre(20, 20, 10, 1);

    // equerres bague haut
    rotate([0,0,90*i]) 
    translate([1,-33,235]) 
    rotate([90,0,0])
    equerre(20, 20, 10, 1);

    rotate([0,0,90*i]) 
    translate([-33,1,235])
    rotate([0,-90,0])
    equerre(20, 20, 10, 1);
    }
}
// Bague de pousée
color("grey")
translate ([0,0,-2])
bague_de_poussee(d_ext, d_int, 54.3, 2, 10);
// Bague milieu
color("grey")
translate ([0,0,160])
bague_creuse(d_int, 50, 10);
// Bague haut
color("grey")
translate ([0,0,225])
bague_creuse(d_int, 50, 10);

// Ailerons
for (aileron = [0:1:3]) {
    rotate([0,0,aileron*90])
    translate([50,0,0])
    union() {
        color("grey")
        translate([-20,-1,0]) 
        cube(size=[20,2,300]);
        aileron(300, 150, 130, 75, 2);
    }
}

/*Systeme retenue propu*/
retenuePropu();

/*Tube*/
color([150/255,150/255,150/255,0.5])
bague_creuse(d_ext, d_int, l_tube);

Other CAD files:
Modelisation3D/Mini_Ailerons-ClementL/roulis.scad
Modelisation3D/Mini_Ailerons-ClementL/lib-gear-dh.scad
Modelisation3D/Mini_Ailerons-ClementL/lib-worm-dh.scad
Modelisation3D/Minuterie-Alexandre/Essai.scad
Modelisation3D/Minuterie-Alexandre/minuterie.scad
Modelisation3D/Module_Vitesse-Dimitri/bloc.stl
Modelisation3D/Module_Vitesse-Dimitri/blocs.scad
Modelisation3D/Module_Vitesse-Dimitri/venturi.scad
Modelisation3D/Module_Vitesse-Dimitri/venturi.stl
Modelisation3D/Module_Vitesse-Dimitri/vitesse.scad
Modelisation3D/Ogive-Dimitri/Ogive.stl
Modelisation3D/Ogive-Dimitri/ogive.scad
Modelisation3D/Ogma/aileron.scad
Modelisation3D/Ogma/arduino.scad
Modelisation3D/Ogma/bagues.scad
Modelisation3D/Ogma/block_ailerons.scad
Modelisation3D/Ogma/block_interrupteur_ogma.scad
Modelisation3D/Ogma/block_rouli.scad
Modelisation3D/Ogma/bras_ogma.scad
Modelisation3D/Ogma/carte_elec.scad
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

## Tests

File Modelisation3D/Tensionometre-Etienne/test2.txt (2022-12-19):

 alpha1
 module ressort(diametre=10, section=1, hauteur=20, nb_spire=10){
    //
    // Mendel90
    //
    // GNU GPL v2
    // nop.head@gmail.com
    // hydraraptor.blogspot.com
    //
    // Springs
    //

    extruder_spring = [ 7,    1, 10, 5];
    hob_spring      = [12, 0.75, 10, 6];

    function spring_od(type)     = type[0];
    function spring_gauge(type)  = type[1];
    function spring_length(type) = type[2];
    function spring_coils(type)  = type[3];

    // taken from openscad example 20
    module coil(r1 = 100, r2 = 10, h = 100, twists)
    {
        hr = h / (twists * 2);
        stepsize = 1/16;
        module segment(i1, i2) {
            alpha1 = i1 * 360*r2/hr;
            alpha2 = i2 * 360*r2/hr;
            len1 = sin(acos(i1*2-1))*r2;
            len2 = sin(acos(i2*2-1))*r2;
            if (len1 < 0.01)
                polygon([
                    [ cos(alpha1)*r1, sin(alpha1)*r1 ],
                    [ cos(alpha2)*(r1-len2), sin(alpha2)*(r1-len2) ],
                    [ cos(alpha2)*(r1+len2), sin(alpha2)*(r1+len2) ]
                ]);
            if (len2 < 0.01)
                polygon([
                    [ cos(alpha1)*(r1+len1), sin(alpha1)*(r1+len1) ],
                    [ cos(alpha1)*(r1-len1), sin(alpha1)*(r1-len1) ],
                    [ cos(alpha2)*r1, sin(alpha2)*r1 ],
                ]);
            if (len1 >= 0.01 && len2 >= 0.01)
                polygon([
                    [ cos(alpha1)*(r1+len1), sin(alpha1)*(r1+len1) ],
                    [ cos(alpha1)*(r1-len1), sin(alpha1)*(r1-len1) ],
                    [ cos(alpha2)*(r1-len2), sin(alpha2)*(r1-len2) ],
                    [ cos(alpha2)*(r1+len2), sin(alpha2)*(r1+len2) ]
                ]);
        }
        linear_extrude(height = h, twist = 180*h/hr,
                $fn = (hr/r2)/stepsize, convexity = 5) {
            for (i = [ stepsize : stepsize : 1+stepsize/2 ])
                segment(i-stepsize, min(i, 1));
        }
    }

    module comp_spring(type, l = 0) {
        l = (l == 0) ? spring_length(type) : l;

        coil(r1 = (spring_od(type) - spring_gauge(type)) / 2, r2 = spring_gauge(type) / 2, h = l, twists = spring_coils(type));

        if($children)
            translate([0, 0, l])
                children();
    }
    
    color("grey")
    comp_spring([diametre, section, hauteur, nb_spire]);
}

// ressort();

module ressort_ogma() {
    // diametre, section, hauteur, nb spire
    ressort(12, 1.5, 30, 8);
}
ressort_ogma();
difference{
    cylinder(1,2,3)
}

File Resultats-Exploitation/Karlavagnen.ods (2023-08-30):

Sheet: Feuille1
Millisecondes depuis demarrage | Tensionometre | Pression | Pression (calculée) | Temps (relatif) | Tensionometre (calibrage polynomial) | Tensionometre (calibrage lineaire) |  | Vitesse (en z) | 96955
1090339 | 0 | 31444 | 438.6 | 0 | 1.35856856034642 | 2.74174218233938 | 3.60000000000002 |  | 65495
1090390 | 0 | 31445 | 438.5 | 51 | 1.35856856034642 | 2.74174218233938 | 3.5
1090440 | 0 | 31445 | 438.5 | 101 | 1.35856856034642 | 2.74174218233938 | 3.5
1090490 | 0 | 31443 | 438.7 | 151 | 1.35856856034642 | 2.74174218233938 | 3.69999999999999
1090540 | 0 | 31444 | 438.6 | 201 | 1.35856856034642 | 2.74174218233938 | 3.60000000000002 | 15.3522607781283
1090590 | 0 | 31445 | 438.5 | 251 | 1.35856856034642 | 2.74174218233938 | 3.5 | 18.1052631578947
1090640 | 0 | 31479 | 435.1 | 301 | 1.35856856034642 | 2.74174218233938 | 0.100000000000023 | 20.3157894736842
1090690 | 0 | 31451 | 437.9 | 351 | 1.35856856034642 | 2.74174218233938 | 2.89999999999998 | 22.421052631579
1090740 | 0 | 31444 | 438.6 | 401 | 1.35856856034642 | 2.74174218233938 | 3.60000000000002 | 25.7894736842105
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

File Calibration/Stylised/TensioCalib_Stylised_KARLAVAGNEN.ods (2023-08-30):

Valeurs mesurées | Masse (kg)
0 | 0
44 | 6,7
125 | 10
230 | 15
375 | 19,7
524 | 24,7
740 | 29,7
780 | 39,4
948 | 49,7

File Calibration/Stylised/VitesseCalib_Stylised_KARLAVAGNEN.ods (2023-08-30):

Pitot
Vitesse (m/s) | Valeurs mesurées | Vitesse (km/h)
0 | 35 | 0
13,8888888888889 | 40 | 50
19,4444444444444 | 45 | 70
25 | 55 | 90
26,3888888888889 | 62 | 95
30,5555555555556 | 65 | 110
36,1111111111111 | 65 | 130
68 | 349 | 244,8
Venturi
Vitesse (m/s) | Valeurs mesurées | Vitesse (km/h)
0 | 36 | 0
15,2777777777778 | 40 | 55
19,4444444444444 | 45 | 70
22,2222222222222 | 50 | 80
23,6111111111111 | 55 | 85
25 | 60 | 90
26,3888888888889 | 62 | 95
27,7777777777778 | 65 | 100
30,5555555555556 | 72 | 110
36,1111111111111 | 85 | 130

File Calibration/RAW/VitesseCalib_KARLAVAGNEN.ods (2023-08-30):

 | Pitot
 | Vitesse (m/s) | Valeur mesurée | Vitesse (km/h)
 | 0 | 35 | 0
 | 13,8888888888889 | 40 | 50
 | 19,4444444444444 | 45 | 70
 | 25 | 55 | 90
60-65 | 26,3888888888889 | 62 | 95
60-70 | 30,5555555555556 | 65 | 110
60-70 | 36,1111111111111 | 65 | 130
 | 68 | 349 | 244,8
 | Venturi
 | Vitesse (m/s) | Valeur mesurée | Vitesse (km/h)
 | 0 | 36 | 0
 | 15,2777777777778 | 40 | 55
 | 19,4444444444444 | 45 | 70
 | 22,2222222222222 | 50 | 80
55-60 | 23,6111111111111 | 55 | 85
 | 25 | 60 | 90
~60 | 26,3888888888889 | 62 | 95
~65 | 27,7777777777778 | 65 | 100
70-75 | 30,5555555555556 | 72 | 110
80-90 | 36,1111111111111 | 85 | 130

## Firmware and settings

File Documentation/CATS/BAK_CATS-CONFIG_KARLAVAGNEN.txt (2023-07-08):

set acc_threshold = 50
set liftoff_detection_agl = 50
set main_altitude = 311
set timer1_start = MAX_V
set timer1_trigger = CUSTOM_1
set timer1_duration = 0
set timer2_start = CALIBRATE
set timer2_trigger = CALIBRATE
set timer2_duration = 0
set timer3_start = CALIBRATE
set timer3_trigger = CUSTOM_2
set timer3_duration = 0
set timer4_start = CALIBRATE
set timer4_trigger = CALIBRATE
set timer4_duration = 0
set ev_calibrate = 0,0,0,0,0,0,0,0,0,0,0,0,0,0,0,0
set ev_ready = 7,1,0,0,0,0,0,0,0,0,0,0,0,0,0,0
set ev_liftoff = 7,2,0,0,0,0,0,0,0,0,0,0,0,0,0,0
set ev_burnout = 0,0,0,0,0,0,0,0,0,0,0,0,0,0,0,0
set ev_apogee = 0,0,0,0,0,0,0,0,0,0,0,0,0,0,0,0
set ev_main_deployment = 0,0,0,0,0,0,0,0,0,0,0,0,0,0,0,0
set ev_touchdown = 7,0,0,0,0,0,0,0,0,0,0,0,0,0,0,0
set ev_custom1 = 5,0,1,1000,5,500,1,1000,5,1000,0,0,0,0,0,0
set ev_custom2 = 6,500,6,1000,0,0,0,0,0,0,0,0,0,0,0,0
set servo1_init_pos = 0
set servo2_init_pos = 0
set tele_link_phrase = reuzia
set tele_test_phrase = reuzia
set tele_power_level = 20
set tele_enable = ON
set tele_adaptive_power = OFF
set buzzer_volume = 100
set battery_type = LI-ION
set rec_elements = 4294967295
set rec_speed = 100Hz
set test_mode = OFF

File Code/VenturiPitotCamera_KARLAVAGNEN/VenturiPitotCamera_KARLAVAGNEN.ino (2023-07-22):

// #define DEBUG
#define ventPin A0
#define pitotPin A1
#define DELAY_MESURE 100 // ms
#define DELAY_SERVO   25 // ms

#include <Servo.h>
#include <SPI.h>
#include <SD.h>

Servo servo;
int angle = 0;

#define ROTATION_POSITIVE true
#define ROTATION_NEGATIVE false
bool servo_sens = ROTATION_POSITIVE;

File dataFile;

unsigned long prev_mes_t    = 0;
unsigned long timestamp_mes = 0;
int val_venturi             = 0;
int val_pito                = 0;

unsigned long prev_servo_t;
unsigned long timestamp_servo;

void writeData(unsigned long timestamp, int pito, int venturi) {
  dataFile.print(timestamp);
  dataFile.print("\t");
  dataFile.print(venturi);
  dataFile.print("\t");
  dataFile.println(pito);
  dataFile.flush();
  #ifdef DEBUG
    Serial.print(timestamp);
    Serial.print("\t");
    Serial.print(venturi);
    Serial.print("\t");
    Serial.println(pito);
  #endif
}

void setup() {
  #ifdef DEBUG
    Serial.begin(9600);
    Serial.println("Initialising...");
  #endif

  servo.attach(9);
  
  SD.begin(10);

  pinMode(ventPin, INPUT);
  pinMode(pitotPin, INPUT);

  dataFile = SD.open("DATA.TXT", FILE_WRITE);

  #ifdef DEBUG
    Serial.println("Done!");
  #endif
}

void loop() {
  timestamp_mes = millis();
  // Mesure pito & venturi
  if ((timestamp_mes - prev_mes_t) >= DELAY_MESURE){
    val_venturi = analogRead(ventPin);
    val_pito    = analogRead(pitotPin);
    writeData(timestamp_mes, val_venturi, val_pito);
    prev_mes_t = timestamp_mes;
  }
  timestamp_servo = timestamp_mes;
  if ((timestamp_servo - prev_servo_t) >= DELAY_SERVO){
    servo.write(angle);
    if (angle == 180)
      servo_sens = ROTATION_NEGATIVE;
    else if (angle == 0)
      servo_sens = ROTATION_POSITIVE;
    if (servo_sens == ROTATION_POSITIVE)
      angle++;
    else
      angle--;
    prev_servo_t = timestamp_servo;
  }
}

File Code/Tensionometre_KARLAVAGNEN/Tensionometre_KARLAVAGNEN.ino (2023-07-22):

#define DEBUG
#define tensioPin A1
#define DELAY_MESURE 50 // ms

#include <Adafruit_BMP085.h>
#include <SPI.h>
#include <SD.h>

Adafruit_BMP085 bmp;
File dataFile;

unsigned long prev_mes_t;
unsigned long timestamp;
int tensioVal;
int pressVal;

void setup() {
  #ifdef DEBUG
    Serial.begin(115200);
    Serial.println("Initialising...");
  #endif

  SD.begin(10);

  bmp.begin();

  pinMode(tensioPin, INPUT);

  dataFile = SD.open("DATA.TXT", FILE_WRITE);

  #ifdef DEBUG
    Serial.println("Done!");
  #endif
}

void loop() {
  timestamp = millis();
  if ((timestamp - prev_mes_t) >= DELAY_MESURE){
    tensioVal = analogRead(tensioPin);
    pressVal = bmp.readPressure();

    #ifdef DEBUG
      if (dataFile) {
        dataFile.print(timestamp);
        dataFile.print("\t");
        dataFile.print(tensioVal);
        dataFile.print("\t");
        dataFile.println(pressVal);
        dataFile.flush();
      }
      else {
        Serial.println("ERROR: Failed to open DATA.TXT");
      }
      Serial.print(timestamp);
      Serial.print("\t");
      Serial.print(tensioVal);
      Serial.print("\t");
      Serial.println(pressVal);
    #else
      dataFile.print(timestamp);
      dataFile.print("\t");
      dataFile.print(tensioVal);
      dataFile.print("\t");
      dataFile.println(pressVal);
      dataFile.flush();
    #endif
    prev_mes_t = timestamp;
  }
}

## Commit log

2022-10-15 ✨ First commit for version control
    [CAO roulis.scad, Essai.scad, Minuterie fusex.scad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]
2022-10-15 🤔Various changes (#1)
    * ^_____^ Nothing's up little update
    * 🧨Delete temporary files
2022-10-22 Add changes (#2)
    * Update
    * Changes integration Alexandre import fix
    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
    [Minuterie fusex.scad, karlavagnen.scad]
2022-10-22 keep up (#3)
    * 🤔Various changes (#1)
    * Add changes (#2)
    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
    [Minuterie fusex.scad, karlavagnen.scad]
2022-10-22 keep up (#3) (#4)
    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
2022-12-19 Merge changes (#8)
    * lol
    * changes
    * changes
    * Add Clement's contribution
    [CAO roulis.scad, Camera dome.scad, Camera ogive.scad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]
2023-05-14 Dev (#12)
    * aaa
    * teub
    ---------
    [Camera dome.scad]
2023-06-04 Dev (#15)
    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
    [Camera dome.scad, camera.scad, karlavagnen.scad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]
2023-06-10 ✨ Improve README (#20)
    * Update README.md
    * Update README.md
2023-06-10 📃Add StabTraj (#21)
    [Stabtraj_KARLAVAGNEN.xlsx]
2023-06-10 Dev (#22)
    * 📃Add StabTraj
    * commit
    [karlavagnen.scad, ogive.scad, roulis.scad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]
2023-06-28 Dev (#23)
    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
2023-07-08 Dev update (#24)
    * VenturiPieces
    * Update StabTraj
    * modificiations venturi
    * Réorganisation + Update
    * Refine folder names + add arduino code
    [Camera ogive.scad, Essai.scad, Liste achats.xlsx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]
2023-07-22 Fin Tarbes (#27)
    * Create Code caméra
    * Add files via upload
    * Delete Code caméra
    * Code Arduino
    * Arduino update
    * aaaaaaa calib
    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
    [BAK_CATS-CONFIG_KARLAVAGNEN.txt, Karlavagnen.ods, ST-(StabTraj)_KARLAVAGNEN.xlsm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]
2023-07-22 Add files via upload (#29)
    [blocs.scad]
2023-07-28 Update calibration files
    [TensioCalib_KARLAVAGNEN.ods, TensioCalib_KARLAVAGNEN_V2.ods, VitesseCalib_KARLAVAGNEN.ods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]
2023-07-28 Update 2 Calibration Files (Cleanup)
    [TensioCalib_Stylised_KARLAVAGNEN.ods, VitesseCalib_KARLAVAGNEN.ods, VitesseCalib_KARLAVAGNEN_FINAL.ods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]
2023-07-29 Update doc and readme
    [TensioCalib_Stylised_KARLAVAGNEN.ods]
2023-08-05 Update OpenSCAD library (rescale images and fix preview)
    [blocs.scad, karlavagnen.scad, vitesse.scad]
2023-08-28 Rapport de projet v2 + actualisation modelisation
    [blocs.scad, karlavagnen.scad, minuterie.scad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]
2023-08-30 FInal update - Rapport de projet
    [Karlavagnen.ods, camera.scad]
2023-08-30 Update README.md - Add Rapport de projet
